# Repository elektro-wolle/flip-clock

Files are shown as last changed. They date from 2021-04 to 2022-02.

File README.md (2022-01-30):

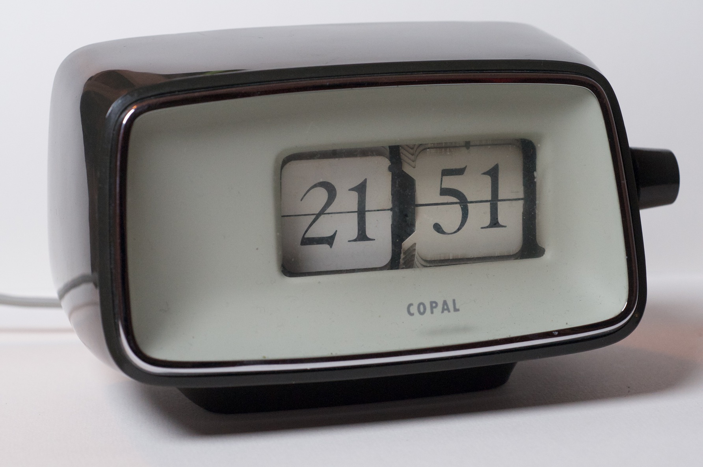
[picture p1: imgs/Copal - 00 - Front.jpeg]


Bei dieser schönen 60er-Jahre Uhr war der Synchronmotor defekt (lief nur
selten an, Versatz von 2h pro Tag). Ein Ersatz für diesen war nicht zu
finden, daher die High-Tech-Variante.

-   Synchronmotor durch Schrittmotor ersetzen

-   Zeit via NTP über einen ESP holen

-   Das Ganze so, dass es ein 1:1 Ersatz zu dem montierten Motor wird

# Herausforderungen

-   Einen Schrittmotor finden mit passendem Ritzel und passender Größe.

-   Der Schrittmotor mit passendem Ritzel ist für max. 5V ausgelegt, die
    üblichen StepSticks brauchen 8V.

-   Alles in das Gehäuse bekommen.

-   Erste Tests zeigten, dass für eine Minute eine unterschiedliche
    Anzahl an Schritten benötigt wird.

-   Keine Möglichkeit, das Umspringen der Minuten zu erkennen.

-   Spontane Abschaltungen bei Netzbetrieb.

# Lösungen

## Schrittmotor

AliExpress sei Dank: [Stepper-Motor mit 12 Zähnen und Modul
0,25](https://www.aliexpress.com/item/4001009328124.html).

## StepStick

Natürlich gibt es was von [Trinamic](https://www.trinamic.com) auf Basis
des [TMC2225
Datasheet](https://www.trinamic.com/fileadmin/assets/Products/ICs_Documents/TMC2225_Datasheet_Rev1.11.pdf).
Zum Beispiel [hier](https://www.amazon.de/dp/B08R3GFYTR).

## Platine produzieren

Millimetergenaues Ausmessen, KiCad, Aisler:

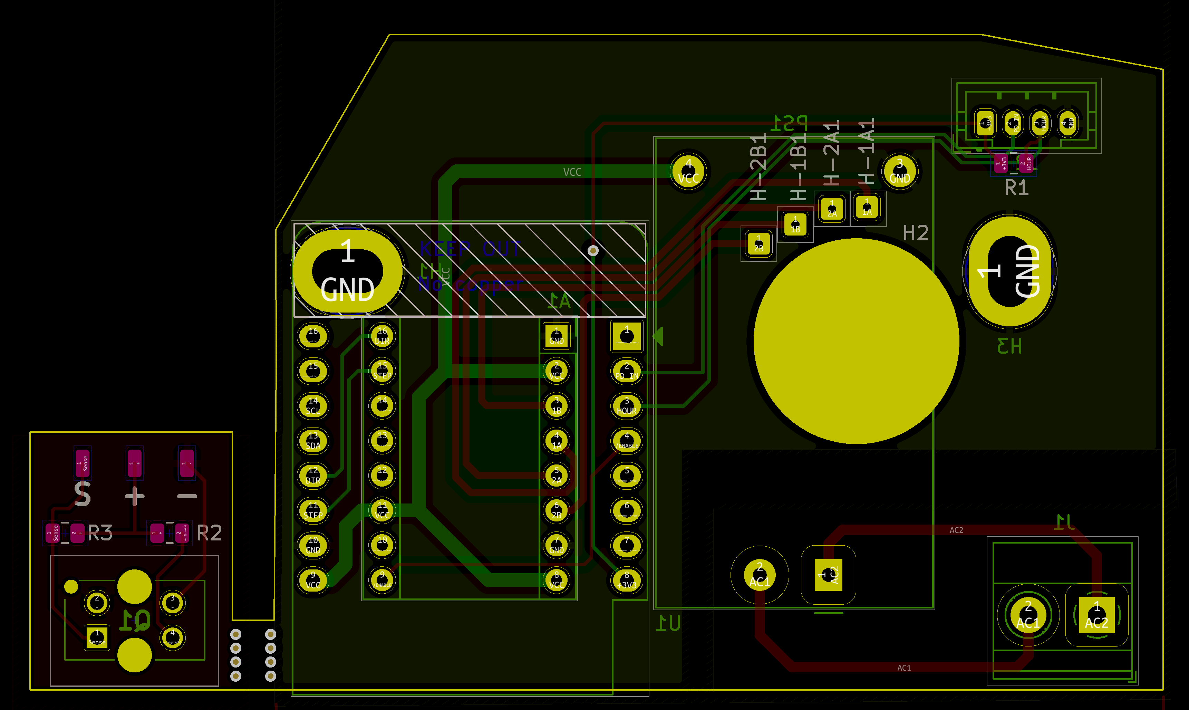
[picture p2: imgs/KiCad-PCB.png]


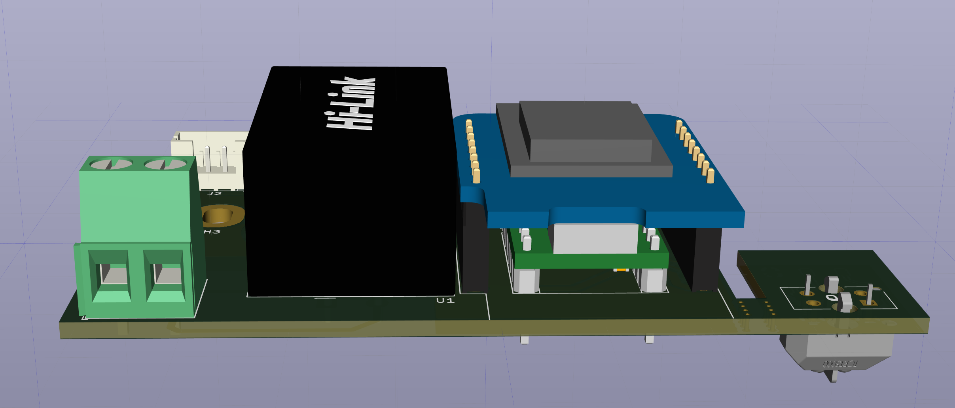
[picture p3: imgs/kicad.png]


## Schritte zählen

Aufgrund des doch sehr beschränkten Platzes, blieb nur die Möglichkeit
übrig, die bestehende Glimmmlampe auszubauen und stattdessen eine kleine
Reflex-Lichtschranke (TCRT-5000) anzubringen. Diese löst recht
zuverlässig auf, wenn sich ein Blatt der Minuten-Anzeige im Fallen
befindet.

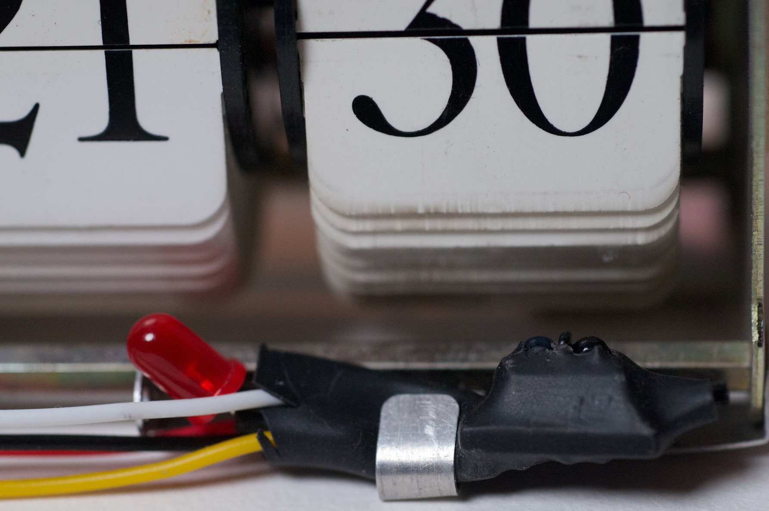
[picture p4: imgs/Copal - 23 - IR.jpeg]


## Spontane Resets

Ein 100uF Kondensator auf der 5V Schiene wirkt Wunder:

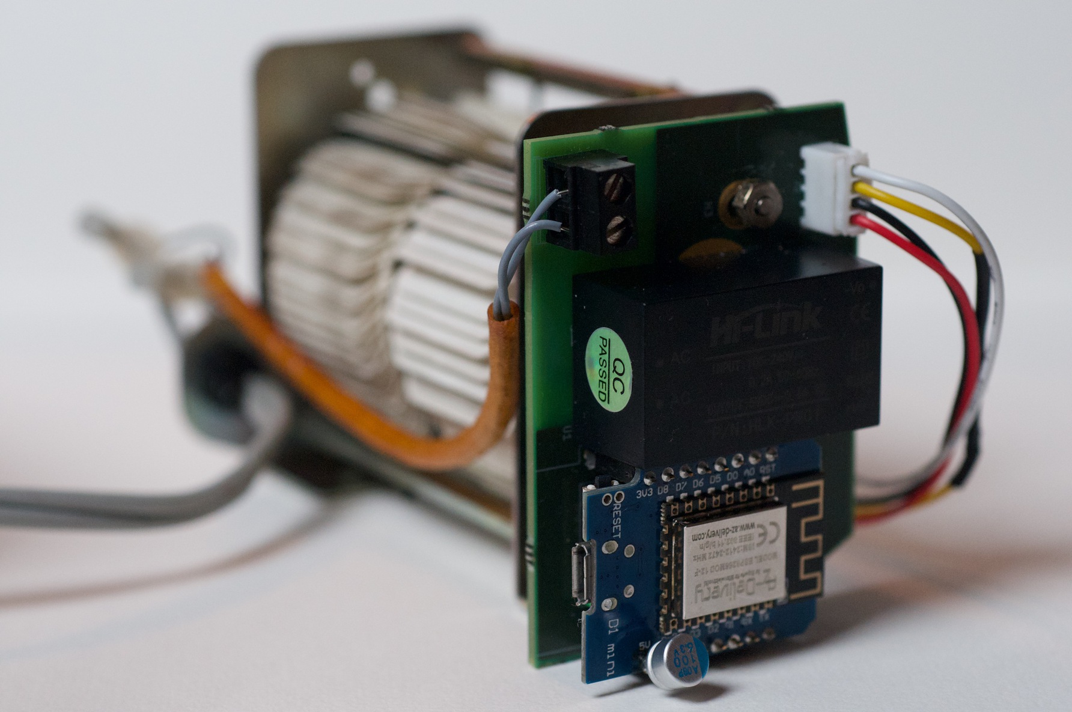
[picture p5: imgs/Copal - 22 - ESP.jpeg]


## Fertiger Aufbau

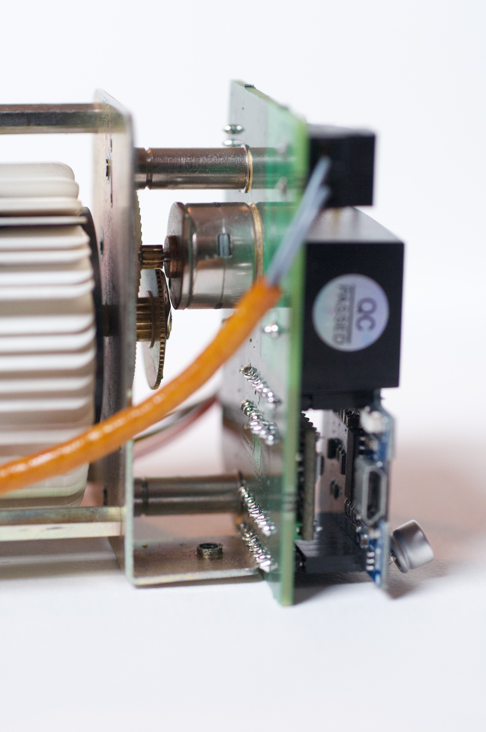
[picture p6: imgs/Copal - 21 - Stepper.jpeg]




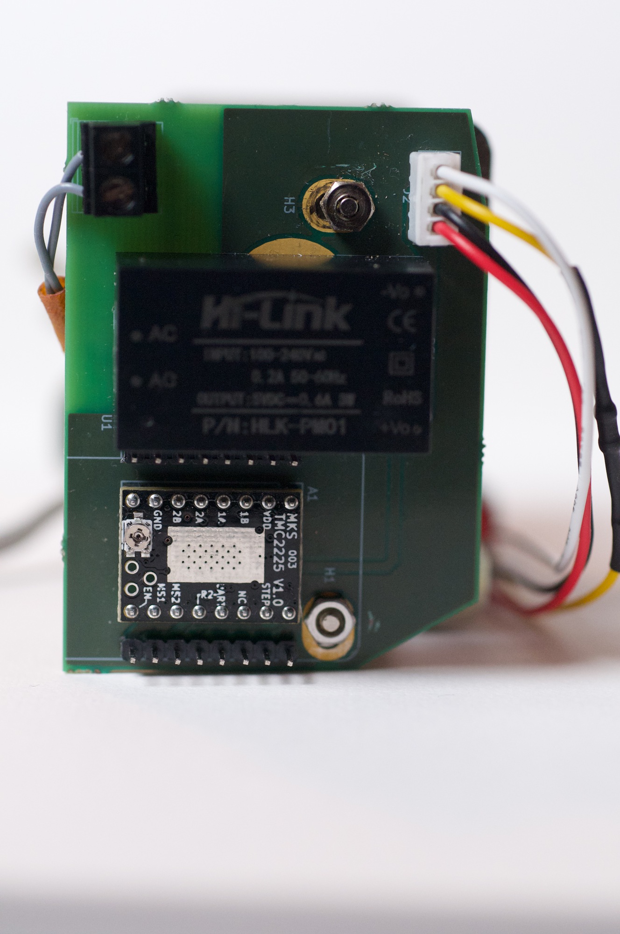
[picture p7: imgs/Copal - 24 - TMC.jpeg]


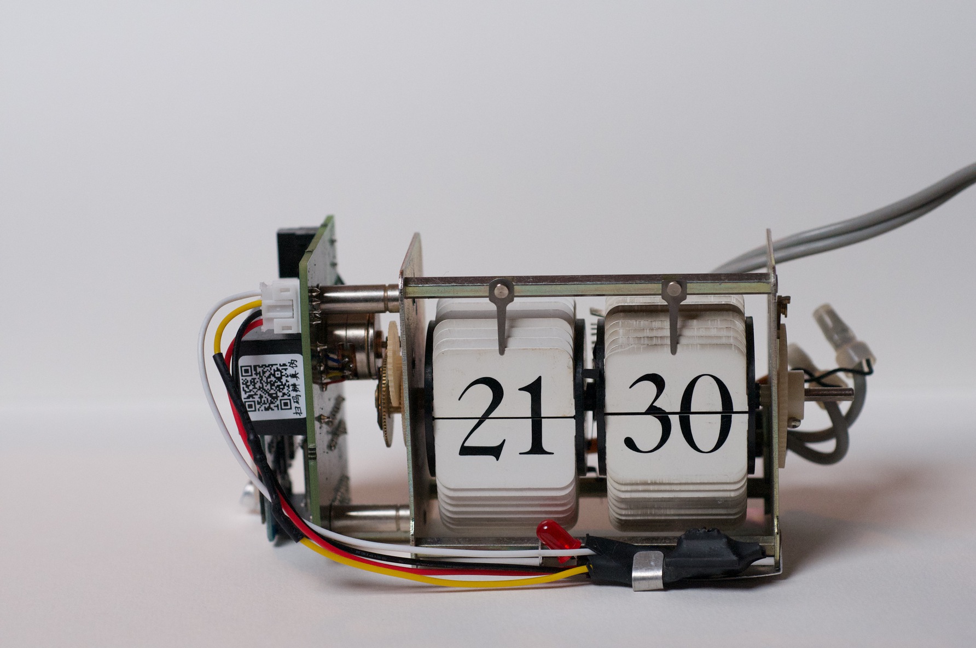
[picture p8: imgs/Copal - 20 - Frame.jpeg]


## Zusammenbau

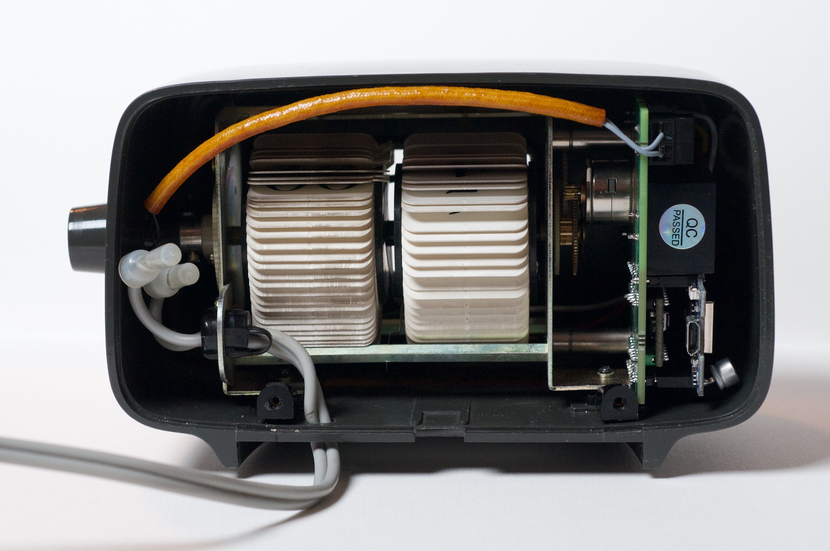
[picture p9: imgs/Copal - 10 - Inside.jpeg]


# Software

Kleines C++ Projekt mit platformio auf Basis der Bibliotheken:
[WiFiManager](https://github.com/tzapu/WiFiManager),
[AceTime](https://github.com/bxparks/AceTime),
[ESP_DoubleResetDetector](https://github.com/khoih-prog/ESP_DoubleResetDetector).

Lösung ist straight-forward: Intern wird die vermutlich angezeigte Zeit
(durch das Zählen via IR-Reflex-Lichtschranke) mit der via NTP
empfangenen Zeit verglichen und solange der Stepper-Motor aktiviert, bis
diese übereinstimmen.

Dabei eine Sonderbehandlung für kleine Abweichungen (bis 10 Minuten wird
einfach gewartet, bis die Zeit übereinstimmt) und in der Nacht (z.B. Bei
der Sommer-/Winterzeit-Umstellung müssten 23 Stunden nach vorne gestellt
werden).

Über eine minimale Web-Oberfläche kann bei Stromausfall oder ähnlichem
die tatsächlich angezeigte Uhrzeit angegeben werden. Code siehe
[Quellcode](sw/src/main.cpp).

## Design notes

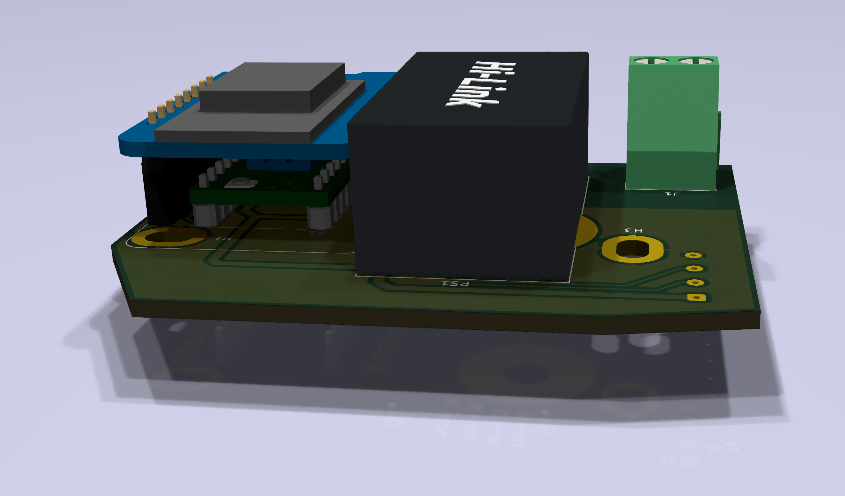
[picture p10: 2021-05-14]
hardware/flip-clock-front.png

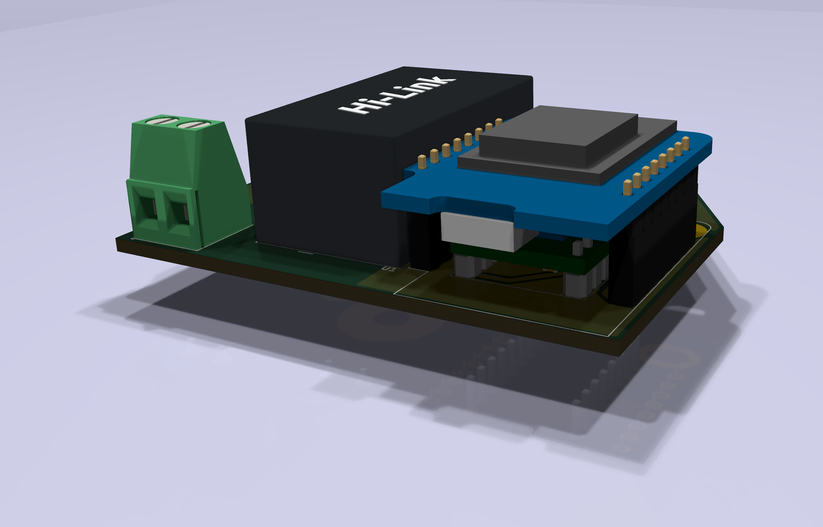
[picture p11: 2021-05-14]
hardware/flip-clock-rear.png

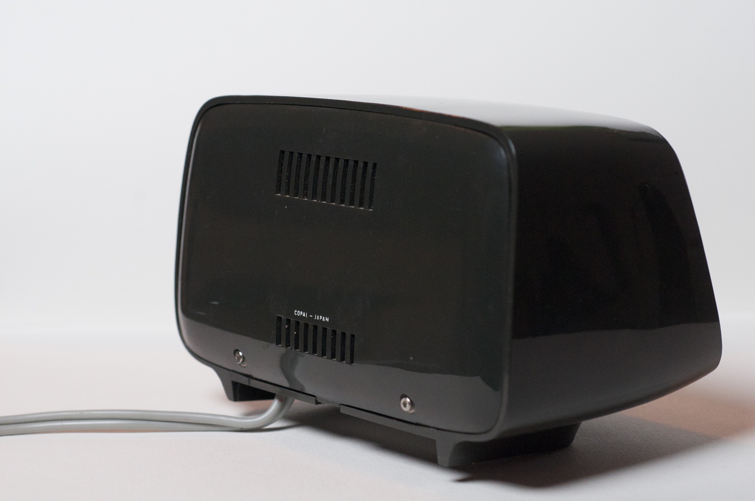
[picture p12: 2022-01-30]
imgs/Copal - 01 - Back.jpeg

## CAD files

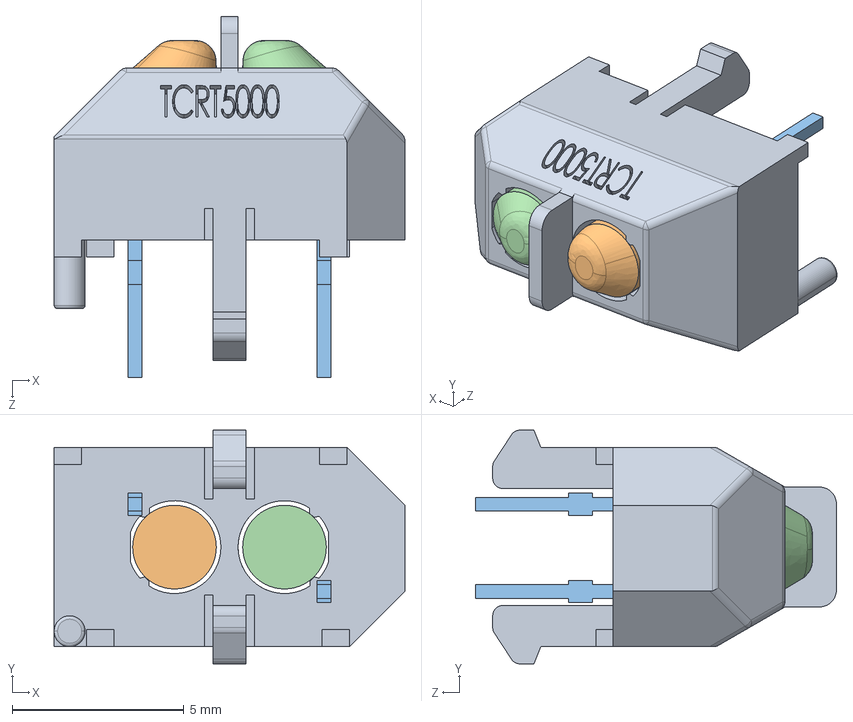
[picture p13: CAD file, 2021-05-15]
hardware/LIB_TCRT5000/TCRT5000/3D/TCRT5000.stp
10.2 x 6.80 x 10.5 mm

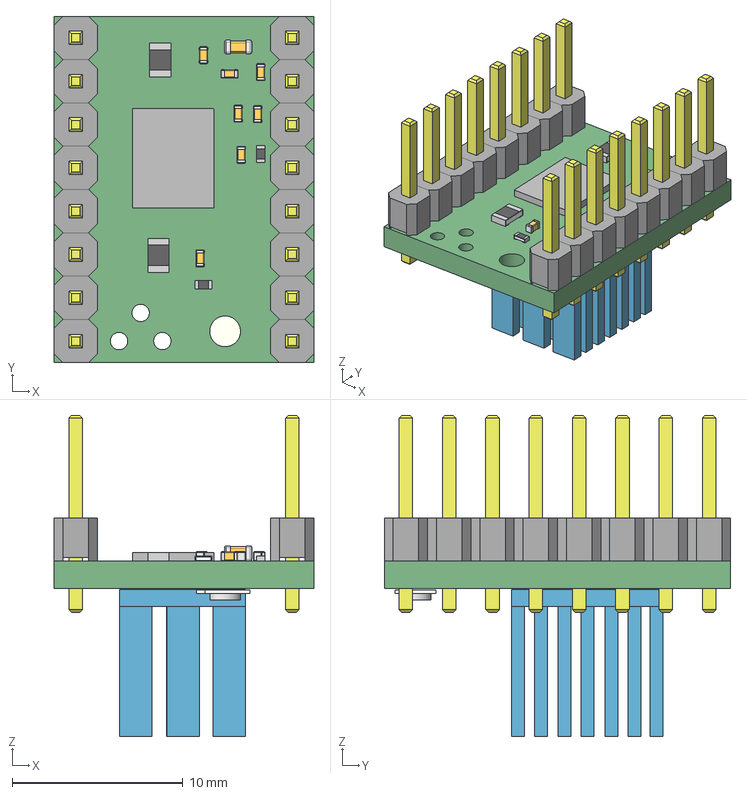
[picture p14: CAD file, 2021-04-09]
hardware/tmc2100.step
15.2 x 20.3 x 18.8 mm
Board
1x08 x 4
R0402 x 8
R0805 x 8
C0603 x 2
C0402 x 14
Extruded x 24

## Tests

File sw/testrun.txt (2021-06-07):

05:07:

begin
[rep=19,min=22,delta=11,avg=1], [rep=34,min=26,delta=201,avg=60], 
done after 34
05:08:

begin
[rep=35,min=26,delta=225,avg=118], 
done after 35
05:09:

begin
[rep=34,min=26,delta=206,avg=83], 
done after 34
05:10:

begin
[rep=0,min=14,delta=11,avg=6], [rep=34,min=29,delta=21,avg=3], [rep=35,min=111,delta=152,avg=104], 
done after 35
05:11:

begin
[rep=16,min=16,delta=14,avg=3], [rep=22,min=12,delta=19,avg=7], [rep=27,min=21,delta=21,avg=3], [rep=38,min=27,delta=213,avg=68], 
done after 38
05:12:

begin
[rep=1,min=20,delta=12,avg=1], [rep=6,min=14,delta=17,avg=5], [rep=12,min=16,delta=16,avg=5], [rep=18,min=20,delta=14,avg=1], [rep=35,min=28,delta=60,avg=7], [rep=36,min=125,delta=126,avg=79], 
done after 36
05:13:

begin
[rep=32,min=28,delta=155,avg=25], 
done after 32
05:14:

begin
[rep=33,min=18,delta=236,avg=122], 
done after 33
05:15:

begin
[rep=37,min=21,delta=224,avg=139], 
done after 37
05:16:

begin
[rep=26,min=23,delta=12,avg=1], [rep=34,min=25,delta=244,avg=169], 
done after 34
05:17:

begin
[rep=35,min=26,delta=228,avg=158], 
done after 35
05:18:

begin
[rep=8,min=17,delta=12,avg=2], [rep=32,min=29,delta=215,avg=103], 
done after 32
05:19:

begin
[rep=35,min=25,delta=192,avg=44], 
done after 35
05:20:

begin
[rep=26,min=15,delta=16,avg=5], [rep=31,min=22,delta=11,avg=1], [rep=37,min=24,delta=18,avg=3], [rep=40,min=28,delta=131,avg=17], 
done after 40
05:21:

begin
[rep=3,min=16,delta=16,avg=2], [rep=8,min=16,delta=12,avg=2], [rep=14,min=13,delta=19,avg=5], [rep=20,min=21,delta=19,avg=3], [rep=25,min=20,delta=18,avg=5], [rep=33,min=27,delta=151,avg=27], 
done after 33
05:22:

begin
[rep=34,min=30,delta=204,avg=51], 
done after 34
05:23:

begin
[rep=35,min=30,delta=115,avg=19], 
done after 35
05:24:

begin
[rep=37,min=29,delta=224,avg=127], 
done after 37
05:25:

begin
[rep=33,min=27,delta=203,avg=102], 
done after 33
05:26:

begin
[rep=0,min=12,delta=11,avg=7], [rep=33,min=23,delta=160,avg=29], 
done after 33
05:27:

begin
[rep=36,min=25,delta=159,avg=31], 
done after 36
05:28:

begin
[rep=37,min=25,delta=60,avg=11], [rep=38,min=124,delta=128,avg=78], 
done after 38
05:29:

begin
[rep=12,min=18,delta=19,avg=4], [rep=17,min=17,delta=13,avg=4], [rep=23,min=25,delta=15,avg=3], [rep=28,min=25,delta=17,avg=3], [rep=34,min=28,delta=212,avg=108], 
done after 34
05:30:

begin
[rep=0,min=12,delta=12,avg=6], [rep=8,min=17,delta=21,avg=11], [rep=33,min=29,delta=227,avg=112], 
done after 33
05:31:

begin
[rep=34,min=29,delta=219,avg=135], 
done after 34
05:32:

begin
[rep=36,min=28,delta=225,avg=155], 
done after 36
05:33:

begin
[rep=34,min=14,delta=190,avg=49], 
done after 34
05:34:

begin
[rep=34,min=35,delta=212,avg=78], 
done after 34
05:35:

begin
[rep=33,min=29,delta=20,avg=9], [rep=34,min=112,delta=136,avg=85], 
done after 34
05:36:

begin
[rep=4,min=17,delta=13,avg=2], [rep=32,min=32,delta=210,avg=79], 
done after 32
05:37:

begin
[rep=37,min=30,delta=213,avg=150], 
done after 37
05:38:

begin
[rep=3,min=18,delta=11,avg=2], [rep=8,min=19,delta=16,avg=1], [rep=14,min=20,delta=17,avg=4], [rep=20,min=25,delta=12,avg=3], [rep=25,min=32,delta=17,avg=2], [rep=35,min=32,delta=158,avg=27], 
done after 35
05:39:

begin
[rep=34,min=35,delta=191,avg=82], 
done after 34
05:40:

begin
[rep=34,min=39,delta=211,avg=131], 
done after 34
05:41:

begin
[rep=32,min=26,delta=208,avg=100], 
done after 32
05:42:

begin
[rep=34,min=20,delta=91,avg=15], 
done after 34
05:43:

begin
[rep=39,min=20,delta=138,avg=24], 
done after 39
05:44:

begin
[rep=32,min=19,delta=207,avg=85], 
done after 32
05:45:

begin
[rep=0,min=12,delta=12,avg=7], [rep=33,min=26,delta=30,avg=6], [rep=34,min=112,delta=121,avg=79], 
done after 34
05:46:

begin
[rep=0,min=13,delta=16,avg=6], [rep=36,min=21,delta=223,avg=106], 
done after 36
05:47:

begin
[rep=3,min=15,delta=17,avg=2], [rep=9,min=14,delta=12,avg=3], [rep=15,min=17,delta=14,avg=1], [rep=20,min=15,delta=20,avg=5], [rep=26,min=22,delta=12,avg=3], [rep=32,min=27,delta=16,avg=2], [rep=35,min=26,delta=126,avg=21], 
done after 35
05:48:

begin
[rep=34,min=24,delta=221,avg=148], 
done after 34
05:49:

begin
[rep=33,min=21,delta=169,avg=36], 
done after 33
05:50:

begin
[rep=21,min=12,delta=19,avg=9], [rep=33,min=43,delta=198,avg=144], 
done after 33
05:51:

begin
[rep=36,min=10,delta=216,avg=126], 
done after 36
05:52:

begin
[rep=34,min=24,delta=200,avg=54], 
done after 34
05:53:

begin
[rep=34,min=14,delta=124,avg=21], 
done after 34
05:54:

begin
[rep=32,min=19,delta=155,avg=30], 
done after 32
05:55:

begin
[rep=35,min=24,delta=208,avg=74], 
done after 35
05:56:

begin
[rep=3,min=14,delta=11,avg=3], [rep=8,min=15,delta=11,avg=1], [rep=14,min=14,delta=20,avg=3], [rep=20,min=11,delta=13,avg=5], [rep=25,min=16,delta=19,avg=3], [rep=31,min=18,delta=19,avg=6], [rep=37,min=22,delta=219,avg=87], 
done after 37
05:57:

begin
[rep=0,min=8,delta=24,avg=12], [rep=36,min=29,delta=220,avg=159], 
done after 36
05:58:

begin
[rep=20,min=21,delta=11,avg=1], [rep=33,min=21,delta=232,avg=158], 
done after 33
05:59:

begin
[rep=33,min=25,delta=175,avg=42], 
done after 33
06:00:

begin
[rep=32,min=23,delta=210,avg=53], 
done after 32
06:01:

begin
[rep=35,min=20,delta=12,avg=8], [rep=36,min=54,delta=190,avg=132], 
done after 36
06:02:

begin
[rep=33,min=21,delta=19,avg=9], [rep=34,min=103,delta=145,avg=89], 
done after 34
06:03:

begin
[rep=34,min=23,delta=207,avg=140], 
done after 34
06:04:

begin
[rep=16,min=17,delta=11,avg=1], [rep=35,min=19,delta=53,avg=10], [rep=36,min=130,delta=119,avg=69], 
done after 36
06:05:

begin
[rep=8,min=15,delta=13,avg=2], [rep=14,min=14,delta=19,avg=3], [rep=19,min=15,delta=12,avg=1], [rep=25,min=11,delta=12,avg=4], [rep=30,min=20,delta=18,avg=1], [rep=33,min=15,delta=215,avg=147], 
done after 33
06:06:

begin
[rep=41,min=20,delta=197,avg=50], 
done after 41
06:07:

begin
[rep=32,min=21,delta=13,avg=7], [rep=33,min=90,delta=151,avg=103], 
done after 33
06:08:

begin
[rep=31,min=26,delta=209,avg=63], 
done after 31
06:09:

begin
[rep=35,min=23,delta=209,avg=128], 
done after 35
06:10:

begin
[rep=34,min=28,delta=24,avg=3], [rep=35,min=118,delta=144,avg=99], 
done after 35
06:11:

begin
[rep=36,min=26,delta=215,avg=74], 
done after 36
06:12:

begin
[rep=34,min=27,delta=201,avg=48], 
done after 34
06:13:

begin
[rep=35,min=26,delta=208,avg=100], 
done after 35
06:14:

begin
[rep=0,min=12,delta=18,avg=7], [rep=5,min=17,delta=11,avg=2], [rep=11,min=13,delta=13,avg=2], [rep=17,min=12,delta=19,avg=2], [rep=22,min=12,delta=16,avg=2], [rep=34,min=11,delta=159,avg=29], 
done after 34
06:15:

begin
[rep=38,min=16,delta=225,avg=122], 
done after 38
06:16:

begin
[rep=32,min=29,delta=73,avg=9], [rep=33,min=146,delta=129,avg=80], 
done after 33
06:17:

begin
[rep=34,min=26,delta=218,avg=90], 
done after 34
06:18:

begin
[rep=34,min=21,delta=186,avg=36], 
done after 34
06:19:

begin
[rep=35,min=27,delta=189,avg=40], 
done after 35
06:20:

begin
[rep=0,min=13,delta=11,avg=6], [rep=36,min=33,delta=216,avg=81], 
done after 36
06:21:

begin
[rep=33,min=22,delta=214,avg=129], 
done after 33
06:22:

begin
[rep=27,min=23,delta=12,avg=2], [rep=37,min=25,delta=121,avg=21], 
done after 37
06:23:

begin
[rep=2,min=17,delta=20,avg=3], [rep=7,min=14,delta=12,avg=4], [rep=13,min=21,delta=11,avg=1], [rep=19,min=22,delta=16,avg=1], [rep=24,min=25,delta=15,avg=2], [rep=37,min=25,delta=216,avg=140], 
done after 37
06:24:

begin
[rep=33,min=20,delta=119,avg=18], 
done after 33
06:25:

begin
[rep=34,min=19,delta=197,avg=87], 
done after 34
06:26:

begin
[rep=27,min=21,delta=12,avg=1], [rep=35,min=15,delta=222,avg=80], 
done after 35
06:27:

begin
[rep=36,min=19,delta=217,avg=130], 
done after 36
06:28:

begin
[rep=33,min=26,delta=208,avg=60], 
done after 33
06:29:

begin
[rep=34,min=25,delta=205,avg=84], 
done after 34
06:30:

begin
[rep=36,min=30,delta=45,avg=8], [rep=37,min=124,delta=133,avg=79], 
done after 37
06:31:

begin
[rep=22,min=20,delta=12,avg=3], [rep=33,min=30,delta=16,avg=2], [rep=36,min=28,delta=217,avg=156], 
done after 36
06:32:

begin
[rep=3,min=18,delta=13,avg=5], [rep=34,min=34,delta=175,avg=27], 
done after 34
06:33:

begin
[rep=33,min=33,delta=198,avg=145], 
done after 33
06:34:

begin
[rep=35,min=35,delta=221,avg=158], 
done after 35
06:35:

begin
[rep=34,min=32,delta=97,avg=13], 
done after 34
06:36:

begin
[rep=34,min=26,delta=225,avg=128], 
done after 34
06:37:

begin
[rep=2,min=11,delta=13,avg=8], [rep=34,min=32,delta=207,avg=143], 
done after 34
06:38:

begin
[rep=33,min=30,delta=228,avg=154], 
done after 33
06:39:

begin
[rep=31,min=33,delta=18,avg=6], [rep=33,min=35,delta=201,avg=101], 
done after 33
06:40:

begin
[rep=4,min=14,delta=15,avg=5], [rep=10,min=16,delta=17,avg=2], [rep=15,min=13,delta=19,avg=6], [rep=21,min=20,delta=18,avg=5], [rep=32,min=34,delta=11,avg=3], [rep=36,min=34,delta=220,avg=109], 
done after 36
06:41:

begin
[rep=34,min=24,delta=88,avg=14], 
done after 34
06:42:

begin
[rep=35,min=24,delta=39,avg=9], [rep=36,min=127,delta=111,avg=68], 
done after 36
06:43:

begin
[rep=36,min=11,delta=137,avg=24], 
done after 36
06:44:

begin
[rep=32,min=19,delta=132,avg=25], 
done after 32
06:45:

begin
[rep=36,min=19,delta=194,avg=55], 
done after 36
06:46:

begin
[rep=35,min=88,delta=175,avg=124], 
done after 35
06:47:

begin
[rep=32,min=27,delta=126,avg=21], 
done after 32
06:48:

begin
[rep=32,min=19,delta=185,avg=42], 
done after 32
06:49:

begin
[rep=0,min=12,delta=20,avg=7], [rep=6,min=17,delta=17,avg=2], [rep=11,min=16,delta=18,avg=2], [rep=17,min=15,delta=12,avg=1], [rep=22,min=17,delta=17,avg=2], [rep=36,min=39,delta=193,avg=144], 
done after 36
06:50:

begin
[rep=35,min=13,delta=217,avg=60], 
done after 35
06:51:

begin
[rep=37,min=48,delta=189,avg=136], 
done after 37
06:52:

begin
[rep=32,min=16,delta=63,avg=8], [rep=33,min=134,delta=112,avg=71], 
done after 33
06:53:

begin
[rep=32,min=17,delta=122,avg=20], 
done after 32
06:54:

begin
[rep=34,min=8,delta=219,avg=125], 
done after 34
06:55:

begin
[rep=35,min=24,delta=59,avg=11], [rep=36,min=140,delta=103,avg=66], 
done after 36
06:56:

begin
[rep=34,min=18,delta=129,avg=23], 
done after 34
06:57:

begin
[rep=16,min=18,delta=18,avg=3], [rep=18,min=14,delta=11,avg=8], [rep=22,min=25,delta=17,avg=2], [rep=28,min=29,delta=12,avg=1], [rep=33,min=26,delta=182,avg=39], 
done after 33
06:58:

begin
[rep=0,min=12,delta=22,avg=8], [rep=6,min=17,delta=17,avg=3], [rep=34,min=20,delta=238,avg=144], 
done after 34
06:59:

begin
[rep=36,min=23,delta=14,avg=9], [rep=37,min=84,delta=146,avg=106], 
done after 37
07:00:

begin
[rep=33,min=32,delta=221,avg=122], 
done after 33
07:01:

begin
[rep=36,min=22,delta=226,avg=149], 
done after 36
07:02:

begin
[rep=32,min=27,delta=226,avg=146], 
done after 32
07:03:

begin
[rep=33,min=18,delta=33,avg=8], [rep=34,min=105,delta=124,avg=77], 
done after 34
07:04:

begin
[rep=35,min=21,delta=226,avg=126], 
done after 35
07:05:

begin
[rep=36,min=55,delta=182,avg=129], 
done after 36
07:06:

begin
[rep=0,min=13,delta=20,avg=6], [rep=6,min=19,delta=19,avg=4], [rep=11,min=16,delta=11,avg=2], [rep=17,min=14,delta=12,avg=4], [rep=23,min=18,delta=16,avg=2], [rep=28,min=22,delta=11,avg=2], [rep=34,min=26,delta=17,avg=2], [rep=37,min=22,delta=204,avg=58], 
done after 37
07:07:

begin
[rep=34,min=20,delta=193,avg=50], 
done after 34
07:08:

begin
[rep=33,min=22,delta=106,avg=16], 
done after 33
07:09:

begin
[rep=37,min=21,delta=34,avg=5], [rep=38,min=114,delta=124,avg=91], 
done after 38
07:10:

begin
[rep=33,min=19,delta=226,avg=69], 
done after 33
07:11:

begin
[rep=33,min=19,delta=205,avg=52], 
done after 33
07:12:

begin
[rep=36,min=23,delta=227,avg=150], 
done after 36
07:13:

begin
[rep=35,min=37,delta=208,avg=97], 
done after 35
07:14:

begin
[rep=26,min=14,delta=11,avg=4], [rep=32,min=31,delta=11,avg=2], [rep=33,min=31,delta=230,avg=83], 
done after 33
07:15:

begin
[rep=4,min=17,delta=13,avg=2], [rep=10,min=14,delta=11,avg=2], [rep=34,min=17,delta=35,avg=4], [rep=35,min=122,delta=124,avg=87], 
done after 35
07:16:

begin
[rep=33,min=22,delta=193,avg=38], 
done after 33
07:17:

begin
[rep=4,min=16,delta=11,avg=1], [rep=15,min=15,delta=12,avg=1], [rep=39,min=24,delta=76,avg=10], [rep=40,min=133,delta=121,avg=78], 
done after 40
07:18:

begin
[rep=33,min=26,delta=218,avg=92], 
done after 33
07:19:

begin
[rep=33,min=23,delta=176,avg=34], 
done after 33
07:20:

begin
[rep=5,min=16,delta=11,avg=1], [rep=36,min=28,delta=229,avg=154], 
done after 36
07:21:

begin
[rep=36,min=26,delta=194,avg=73], 
done after 36
07:22:

begin
[rep=34,min=27,delta=204,avg=51], 
done after 34
07:23:

begin
[rep=29,min=18,delta=13,avg=5], [rep=34,min=21,delta=216,avg=128], 
done after 34
07:24:

begin
[rep=1,min=14,delta=19,avg=6], [rep=7,min=16,delta=17,avg=2], [rep=12,min=14,delta=14,avg=3], [rep=18,min=14,delta=14,avg=4], [rep=24,min=12,delta=21,avg=7], [rep=29,min=23,delta=16,avg=1], [rep=35,min=33,delta=12,avg=2], [rep=36,min=26,delta=215,avg=76], 
done after 36
07:25:

begin
[rep=37,min=22,delta=208,avg=108], 
done after 37
07:26:

begin
[rep=34,min=22,delta=64,avg=12], [rep=35,min=116,delta=137,avg=89], 
done after 35
07:27:

begin
[rep=33,min=24,delta=212,avg=142], 
done after 33
07:28:

begin
[rep=34,min=25,delta=212,avg=87], 
done after 34
07:29:

begin
[rep=36,min=26,delta=213,avg=145], 
done after 36
07:30:

begin
[rep=35,min=31,delta=230,avg=145], 
done after 35
07:31:

begin
[rep=33,min=27,delta=222,avg=157], 
done after 33
07:32:

begin
[rep=34,min=28,delta=228,avg=124], 
done after 34
07:33:

begin
[rep=10,min=15,delta=15,avg=1], [rep=16,min=13,delta=23,avg=7], [rep=22,min=21,delta=16,avg=2], [rep=27,min=23,delta=19,avg=4], [rep=33,min=34,delta=16,avg=2], [rep=35,min=33,delta=29,avg=5], [rep=36,min=124,delta=110,avg=70], 
done after 36
07:34:

begin
[rep=3,min=19,delta=11,avg=1], [rep=37,min=32,delta=216,avg=79], 
done after 37
07:35:

begin
[rep=33,min=31,delta=88,avg=11], 
done after 33
07:36:

begin
[rep=0,min=12,delta=11,avg=7], [rep=32,min=32,delta=196,avg=45], 
done after 32
07:37:

begin
[rep=33,min=28,delta=45,avg=10], [rep=34,min=128,delta=117,avg=69], 
done after 34
07:38:

begin
[rep=33,min=25,delta=232,avg=145], 
done after 33
07:39:

begin
[rep=35,min=30,delta=89,avg=14], 
done after 35
07:40:

begin
[rep=35,min=36,delta=26,avg=3], [rep=36,min=95,delta=158,avg=95], 
done after 36
07:41:

begin
[rep=32,min=25,delta=218,avg=113], 
done after 32
07:42:

begin
[rep=7,min=15,delta=15,avg=3], [rep=13,min=16,delta=12,avg=2], [rep=19,min=15,delta=22,avg=6], [rep=24,min=19,delta=16,avg=2], [rep=30,min=21,delta=18,avg=3], [rep=32,min=19,delta=159,avg=31], 
done after 32
07:43:

begin
[rep=41,min=13,delta=205,avg=136], 
done after 41
07:44:

begin
[rep=34,min=15,delta=60,avg=9], [rep=35,min=127,delta=114,avg=80], 
done after 35
07:45:

begin
[rep=33,min=24,delta=123,avg=21], 
done after 33
07:46:

begin
[rep=33,min=20,delta=134,avg=22], 
done after 33
07:47:

begin
[rep=33,min=25,delta=183,avg=51], 
done after 33
07:48:

begin
[rep=34,min=22,delta=195,avg=47], 
done after 34
07:49:

begin
[rep=35,min=15,delta=28,avg=5], [rep=36,min=96,delta=136,avg=98], 
done after 36
07:50:

begin
[rep=33,min=11,delta=236,avg=165], 
done after 33
07:51:

begin
[rep=2,min=16,delta=16,avg=3], [rep=8,min=14,delta=23,avg=6], [rep=14,min=18,delta=16,avg=1], [rep=19,min=13,delta=23,avg=6], [rep=25,min=21,delta=14,avg=4], [rep=33,min=22,delta=87,avg=13], 
done after 33
07:52:

begin
[rep=34,min=15,delta=215,avg=87], 
done after 34
07:53:

begin
[rep=37,min=17,delta=25,avg=8], [rep=38,min=97,delta=139,avg=103], 
done after 38
07:54:

begin
[rep=34,min=14,delta=232,avg=140], 
done after 34
07:55:

begin
[rep=34,min=24,delta=174,avg=35], 
done after 34
07:56:

begin
[rep=33,min=20,delta=230,avg=158], 
done after 33
07:57:

begin
[rep=11,min=21,delta=12,avg=1], [rep=35,min=35,delta=125,avg=20], 
done after 35
07:58:

begin
[rep=33,min=20,delta=223,avg=109], 
done after 33
07:59:

begin
[rep=33,min=27,delta=11,avg=5], [rep=34,min=33,delta=17,avg=1], [rep=36,min=26,delta=191,avg=93], 
done after 36
08:00:

begin
[rep=3,min=15,delta=18,avg=4], [rep=9,min=12,delta=22,avg=7], [rep=26,min=22,delta=11,avg=6], [rep=31,min=31,delta=13,avg=2], [rep=32,min=28,delta=218,avg=143], 
done after 32
08:01:

begin
[rep=34,min=17,delta=186,avg=40], 
done after 34
08:02:

begin
[rep=33,min=23,delta=226,avg=145], 
done after 33
08:03:

begin
[rep=0,min=14,delta=11,avg=6], [rep=17,min=9,delta=12,avg=1], [rep=38,min=-2,delta=213,avg=112], 
done after 38
08:04:

begin
[rep=36,min=19,delta=165,avg=30], 
done after 36
08:05:

begin
[rep=33,min=20,delta=215,avg=138], 
done after 33
08:06:

begin
[rep=0,min=11,delta=12,avg=7], [rep=37,min=22,delta=211,avg=76], 
done after 37
08:07:

begin
[rep=34,min=14,delta=208,avg=87], 
done after 34
08:08:

begin
[rep=34,min=22,delta=11,avg=6], [rep=35,min=47,delta=204,avg=146], 
done after 35
08:09:

begin
[rep=7,min=19,delta=12,avg=2], [rep=13,min=15,delta=18,avg=5], [rep=19,min=19,delta=16,avg=1], [rep=30,min=22,delta=16,avg=2], [rep=34,min=22,delta=209,avg=91], 
done after 34
08:10:

begin
[rep=1,min=19,delta=15,avg=1], [rep=7,min=12,delta=19,avg=4], [rep=13,min=10,delta=12,avg=4], [rep=35,min=23,delta=238,avg=126], 
done after 35
08:11:

begin
[rep=36,min=24,delta=171,avg=34], 
done after 36
08:12:

begin
[rep=36,min=20,delta=144,avg=21], 
done after 36
08:13:

begin
[rep=33,min=25,delta=211,avg=151], 
done after 33
08:14:

begin
[rep=31,min=17,delta=110,avg=14], 
done after 31
08:15:

begin
[rep=38,min=19,delta=223,avg=170], 
done after 38
08:16:

begin
[rep=34,min=54,delta=216,avg=159], 
done after 34
08:17:

begin
[rep=34,min=23,delta=78,avg=11], [rep=35,min=120,delta=136,avg=85], 
done after 35
08:18:

begin
[rep=11,min=12,delta=11,avg=4], [rep=23,min=21,delta=12,avg=2], [rep=28,min=24,delta=22,avg=5], [rep=32,min=25,delta=234,avg=163], 
done after 32
08:19:

begin
[rep=2,min=20,delta=15,avg=2], [rep=7,min=15,delta=18,avg=2], [rep=34,min=21,delta=122,avg=18], 
done after 34
08:20:

begin
[rep=41,min=30,delta=229,avg=115], 
done after 41
08:21:

begin
[rep=33,min=25,delta=11,avg=6], [rep=34,min=42,delta=200,avg=137], 
done after 34
08:22:

begin
[rep=33,min=28,delta=203,avg=50], 
done after 33
08:23:

begin
[rep=36,min=26,delta=214,avg=144], 
done after 36
08:24:

begin
[rep=36,min=30,delta=222,avg=104], 
done after 36
08:25:

begin
[rep=33,min=24,delta=197,avg=83], 
done after 33
08:26:

begin
[rep=33,min=18,delta=13,avg=9], [rep=34,min=44,delta=208,avg=152], 
done after 34
08:27:

begin
[rep=3,min=19,delta=13,avg=1], [rep=9,min=15,delta=22,avg=6], [rep=20,min=16,delta=18,avg=5], [rep=26,min=22,delta=15,avg=2], [rep=31,min=22,delta=20,avg=7], [rep=36,min=23,delta=203,avg=65], 
done after 36
08:28:

begin
[rep=1,min=19,delta=18,avg=2], [rep=37,min=28,delta=210,avg=67], 
done after 37
08:29:

begin
[rep=34,min=25,delta=121,avg=16], 
done after 34
08:30:

begin
[rep=33,min=29,delta=194,avg=40], 
done after 33
08:31:

begin
[rep=34,min=28,delta=30,avg=4], [rep=35,min=120,delta=127,avg=83], 
done after 35
08:32:

begin
[rep=35,min=28,delta=160,avg=25], 
done after 35
08:33:

begin
[rep=34,min=28,delta=199,avg=52], 
done after 34
08:34:

begin
[rep=34,min=33,delta=227,avg=141], 
done after 34
08:35:

begin
[rep=33,min=32,delta=224,avg=108], 
done after 33
08:36:

begin
[rep=8,min=25,delta=15,avg=2], [rep=20,min=30,delta=11,avg=1], [rep=25,min=31,delta=17,avg=3], [rep=31,min=41,delta=15,avg=3], [rep=32,min=36,delta=169,avg=33], 
done after 32
08:37:

begin
[rep=5,min=14,delta=18,avg=2], [rep=37,min=28,delta=211,avg=109], 
done after 37
08:38:

begin
[rep=36,min=29,delta=226,avg=135], 
done after 36
08:39:

begin
[rep=34,min=-5,delta=206,avg=121], 
done after 34
08:40:

begin
[rep=34,min=43,delta=218,avg=143], 
done after 34
08:41:

begin
[rep=31,min=27,delta=100,avg=16], 
done after 31
08:42:

begin
[rep=35,min=18,delta=204,avg=74], 
done after 35
08:43:

begin
[rep=0,min=20,delta=11,avg=8], [rep=39,min=44,delta=169,avg=38], 
done after 39
08:44:

begin
[rep=17,min=15,delta=18,avg=5], [rep=18,min=10,delta=22,avg=7], [rep=32,min=17,delta=222,avg=146], 
done after 32
08:45:

begin
[rep=14,min=12,delta=12,avg=4], [rep=15,min=16,delta=19,avg=1], [rep=20,min=19,delta=12,avg=1], [rep=26,min=19,delta=19,avg=5], [rep=31,min=24,delta=20,avg=4], [rep=32,min=27,delta=19,avg=2], [rep=33,min=23,delta=196,avg=75], 
done after 33
08:46:

begin
[rep=4,min=15,delta=16,avg=3], [rep=36,min=19,delta=239,avg=156], 
done after 36
08:47:

begin
[rep=35,min=27,delta=185,avg=56], 
done after 35
08:48:

begin
[rep=1,min=19,delta=13,avg=1], [rep=34,min=24,delta=207,avg=93], 
done after 34
08:49:

begin
[rep=34,min=17,delta=220,avg=129], 
done after 34
08:50:

begin
[rep=33,min=19,delta=233,avg=144], 
done after 33
08:51:

begin
[rep=35,min=15,delta=12,avg=6], [rep=36,min=32,delta=201,avg=144], 
done after 36
08:52:

begin
[rep=34,min=19,delta=209,avg=65], 
done after 34
08:53:

begin
[rep=34,min=14,delta=187,avg=46], 
done after 34
08:54:

begin
[rep=16,min=21,delta=14,avg=1], [rep=27,min=24,delta=13,avg=2], [rep=32,min=19,delta=113,avg=21], 
done after 32
08:55:

begin
[rep=1,min=19,delta=19,avg=3], [rep=6,min=16,delta=13,avg=2], [rep=12,min=28,delta=18,avg=3], [rep=35,min=40,delta=204,avg=96], 
done after 35
08:56:

begin
[rep=36,min=21,delta=220,avg=90], 
done after 36
08:57:

begin
[rep=36,min=28,delta=181,avg=39], 
done after 36
08:58:

begin
[rep=34,min=21,delta=231,avg=168], 
done after 34
08:59:

begin
[rep=33,min=27,delta=188,avg=86], 
done after 33
09:00:

begin
[rep=19,min=21,delta=11,avg=2], [rep=33,min=27,delta=224,avg=150], 
done after 33
09:01:

begin
[rep=35,min=25,delta=218,avg=143], 
done after 35
09:02:

begin
[rep=2,min=18,delta=12,avg=1], [rep=33,min=8,delta=112,avg=16], 
done after 33
09:03:

begin
[rep=31,min=15,delta=14,avg=2], [rep=36,min=12,delta=216,avg=122], 
done after 36
09:04:

begin
[rep=0,min=11,delta=19,avg=6], [rep=6,min=17,delta=18,avg=4], [rep=12,min=13,delta=17,avg=2], [rep=36,min=21,delta=212,avg=87], 
done after 36
09:05:

begin
[rep=33,min=19,delta=75,avg=13], [rep=34,min=124,delta=110,avg=69], 
done after 34
09:06:

begin
[rep=41,min=18,delta=13,avg=10], [rep=42,min=110,delta=133,avg=89], 
done after 42
09:07:

begin
[rep=31,min=21,delta=204,avg=72], 
done after 31
09:08:

begin
[rep=4,min=16,delta=11,avg=1], [rep=31,min=24,delta=209,avg=76], 
done after 31
09:09:

begin
[rep=34,min=21,delta=128,avg=20], 
done after 34
09:10:

begin
[rep=36,min=24,delta=236,avg=156], 
done after 36
09:11:

begin
[rep=36,min=44,delta=213,avg=159], 
done after 36
09:12:

begin
[rep=14,min=27,delta=20,avg=9], [rep=20,min=28,delta=19,avg=6], [rep=25,min=36,delta=20,avg=2], [rep=31,min=42,delta=16,avg=2], [rep=34,min=43,delta=48,avg=5], [rep=35,min=154,delta=114,avg=71], 
done after 35
09:13:

begin
[rep=2,min=18,delta=17,avg=2], [rep=35,min=27,delta=212,avg=148], 
done after 35
09:14:

begin
[rep=33,min=14,delta=226,avg=86], 
done after 33
09:15:

begin
[rep=37,min=17,delta=127,avg=16], 
done after 37
09:16:

begin
[rep=32,min=25,delta=23,avg=7], [rep=33,min=118,delta=154,avg=103], 
done after 33
09:17:

begin
[rep=34,min=23,delta=229,avg=117], 
done after 34
09:18:

begin
[rep=34,min=32,delta=187,avg=38], 
done after 34
09:19:

begin
[rep=35,min=25,delta=186,avg=40], 
done after 35
09:20:

begin
[rep=36,min=35,delta=91,avg=9], 
done after 36
09:21:

begin
[rep=7,min=10,delta=17,avg=4], [rep=12,min=8,delta=16,avg=3], [rep=18,min=11,delta=15,avg=3], [rep=24,min=17,delta=12,avg=2], [rep=29,min=23,delta=17,avg=3], [rep=33,min=24,delta=190,avg=53], 
done after 33
09:22:

begin
[rep=38,min=27,delta=225,avg=143], 
done after 38
09:23:

begin
[rep=36,min=32,delta=196,avg=81], 
done after 36
09:24:

begin
[rep=34,min=62,delta=193,avg=135], 
done after 34
09:25:

begin
[rep=33,min=22,delta=195,avg=84], 
done after 33
09:26:

begin
[rep=35,min=20,delta=206,avg=50], 
done after 35
09:27:

begin
[rep=36,min=24,delta=213,avg=135], 
done after 36
09:28:

begin
[rep=33,min=29,delta=196,avg=47], 
done after 33
09:29:
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

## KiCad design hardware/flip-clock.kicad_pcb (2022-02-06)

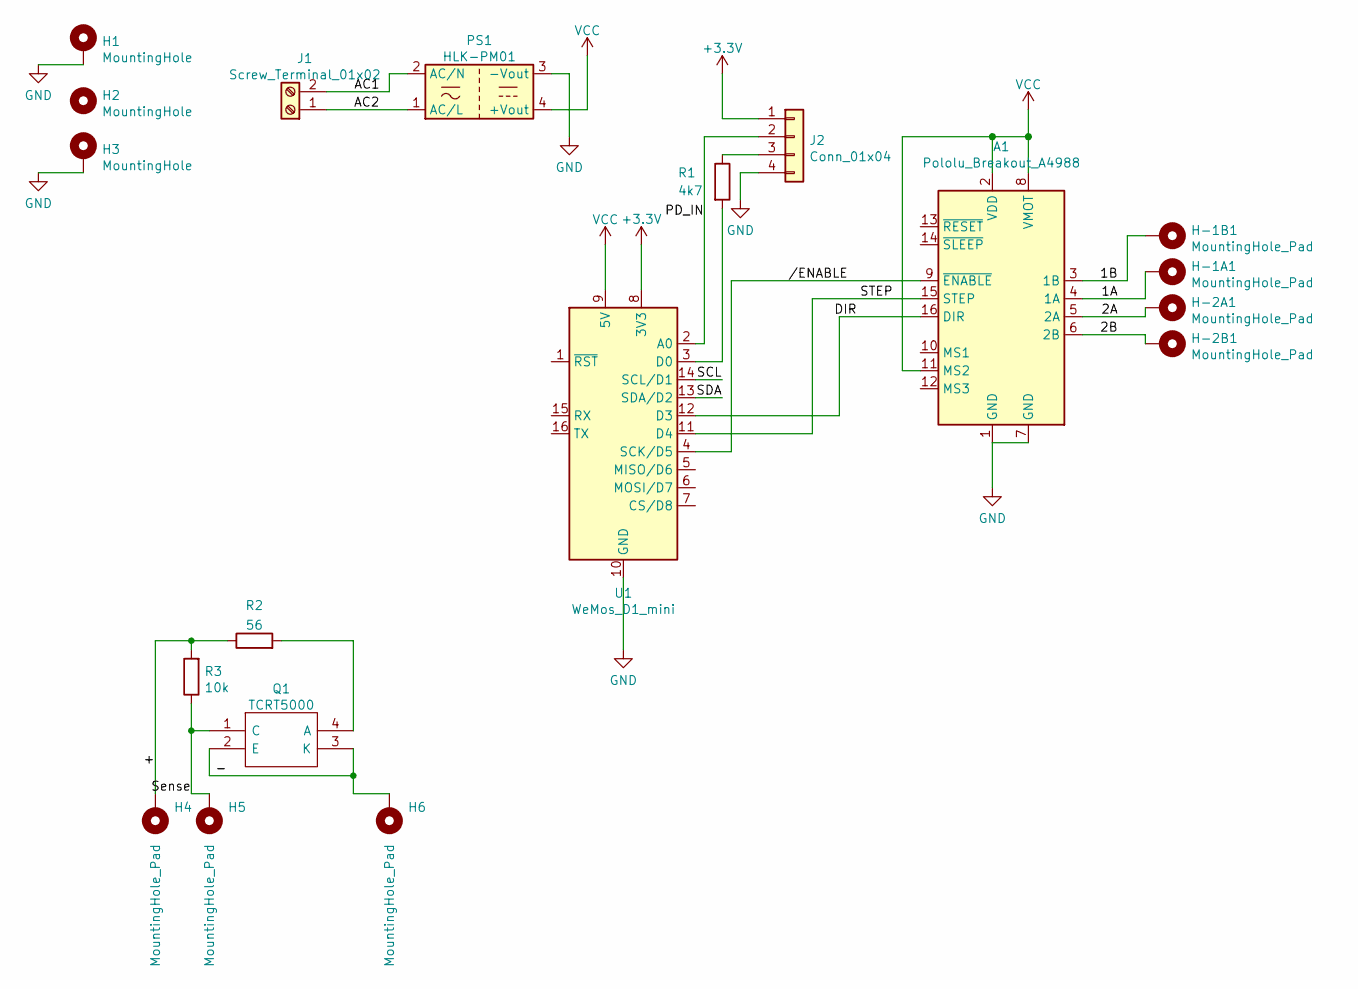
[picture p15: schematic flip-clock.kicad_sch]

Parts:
A1: Pololu_Breakout_A4988; Pololu_Breakout-16_15.2x20.3mm
H1, H3: MountingHole; MountingHole_3.2mm_M3_Pad
H2: MountingHole; MountingHole_5.3mm_M5
H4, H5, H6: MountingHole_Pad; SolderWirePad_1x01_SMD_1x2mm
H-1A1, H-1B1, H-2A1, H-2B1: MountingHole_Pad; SolderWire-0.1sqmm_1x01_D0.4mm_OD1mm
J1: Screw_Terminal_01x02; TerminalBlock_Phoenix_MKDS-1,5-2_1x02_P5.00mm_Horizontal
J2: Conn_01x04; JST_PH_B4B-PH-K_1x04_P2.00mm_Vertical
PS1: HLK-PM01; Converter_ACDC_HiLink_HLK-PMxx
Q1: TCRT5000; Manufacturer_Part_Number TCRT5000; Mouser Part Number 782-TCRT5000
R1: 4k7; R_0805_2012Metric
R2: 56; R_0805_2012Metric
R3: 10k; R_0805_2012Metric
U1: WeMos_D1_mini; WEMOS_D1_mini_light

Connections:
+3V3: J2.1, U1.8 (3V3)
/1A: A1.4 (1A), H-1A1.1
/1B: A1.3 (1B), H-1B1.1
/2A: A1.5 (2A), H-2A1.1
/2B: A1.6 (2B), H-2B1.1
/+: H4.1, R2.1, R3.2
/-: H6.1, Q1.2 (E), Q1.3 (K)
/AC1: J1.2, PS1.2 (AC/N)
/AC2: J1.1, PS1.1 (AC/L)
/DIR: A1.16 (DIR), U1.12 (D3)
/PD_IN: J2.2, U1.2 (A0)
/SCL: U1.14 (SCL/D1)
/SDA: U1.13 (SDA/D2)
/STEP: A1.15 (STEP), U1.11 (D4)
/Sense: H5.1, Q1.1 (C), R3.1
//ENABLE: A1.9 (~ENABLE), U1.4 (SCK/D5)
GND: A1.1 (GND), A1.7 (GND), H1.1, H3.1, J2.4, PS1.3 (-Vout), U1.10 (GND)
unnamed: J2.3, R1.1
unnamed: Q1.4 (A), R2.2
unnamed: R1.2, U1.3 (D0)
VCC: A1.2 (VDD), A1.8 (VMOT), A1.11 (MS2), PS1.4 (+Vout), U1.9 (5V)

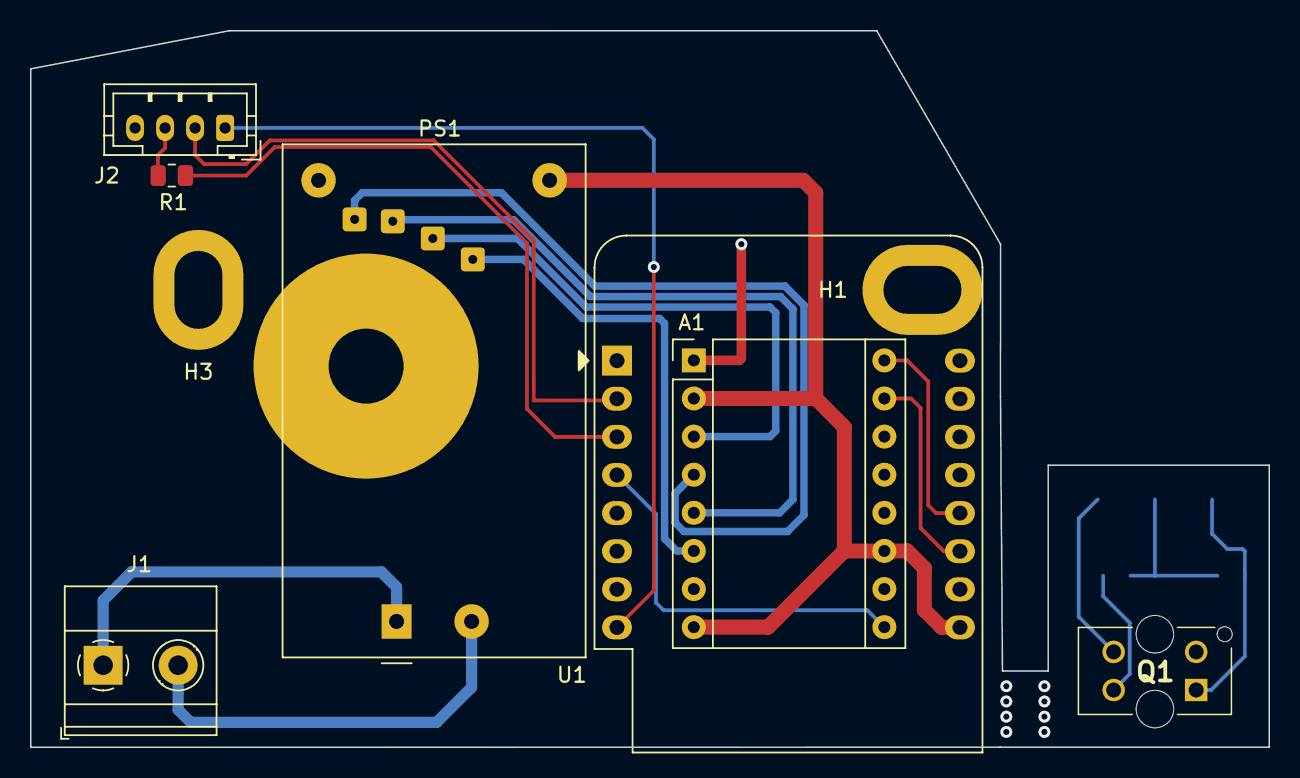
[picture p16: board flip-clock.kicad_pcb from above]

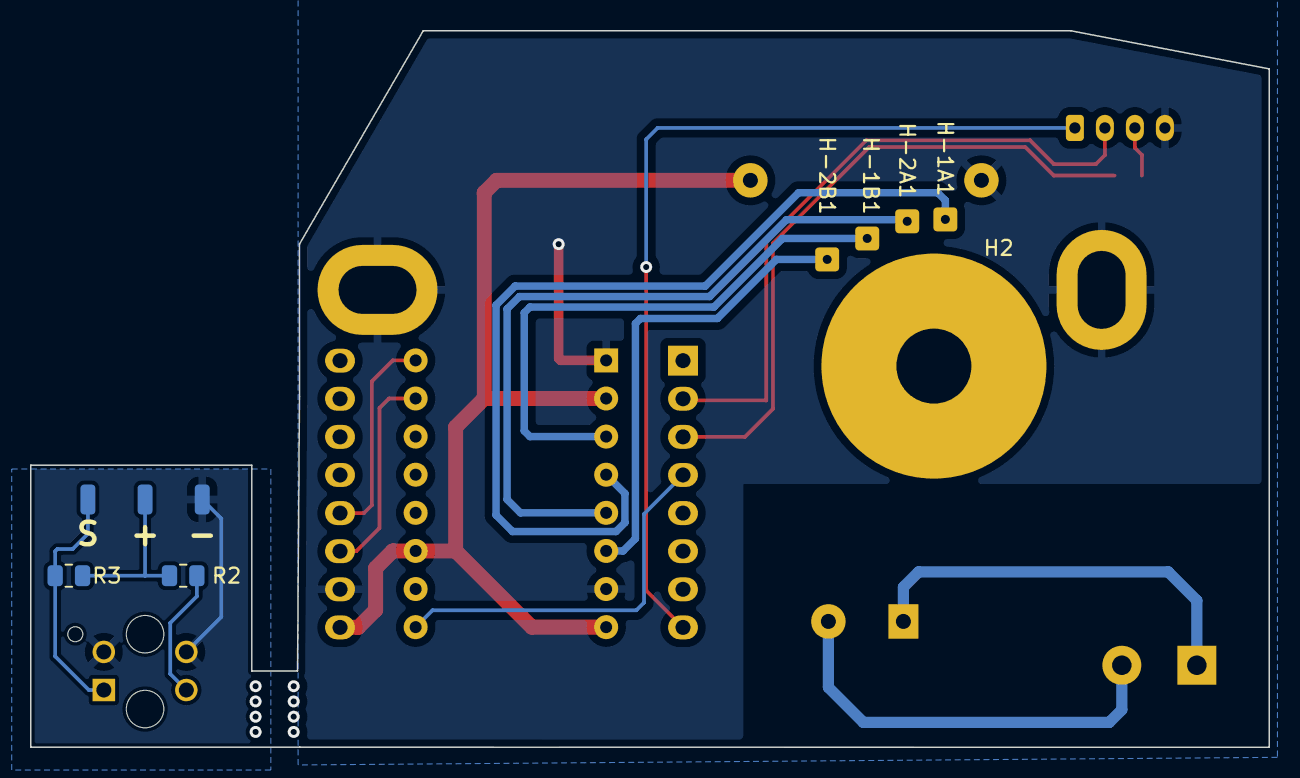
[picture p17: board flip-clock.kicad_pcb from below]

Board: 2 copper layers, 82.6 x 47.8 mm, 19 parts (6 on the bottom side), 19 nets.

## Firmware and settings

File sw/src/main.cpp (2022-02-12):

#include <Arduino.h>

#define ESP_DRD_USE_EEPROM true

#include <ArduinoOTA.h>
#include <DNSServer.h>
#include <ESP8266WebServer.h>
#include <ESP8266WiFi.h>
#include <ESP8266mDNS.h>
#include <ESP_DoubleResetDetector.h>
#include <WiFiManager.h>
#include <WiFiUdp.h>

#include <AceTime.h>

#include <list>

#define OTA 1

#if !defined(NTP_SERVER)
#define NTP_SERVER "pool.ntp.org"
#endif

#define DEBUG 1

#define STATS_ADDRESS 10
#define DRD_ADDRESS 4
#define EEPROM_MAGIC_NUMBER 0xdeadbeed
#define MAX_STEPS_PER_FLIP 40

typedef struct {
    uint32_t magicNumber;
    uint32_t uptimeSeconds;
    uint32_t uptimeSecondsTotal;
    uint32_t previousSecondsTotal;
    uint16_t reboots;
    uint16_t skipped;
    uint16_t skippedTotal;
    uint32_t previousSkippedTotal;
    uint32_t zoneId;
} statistics_t;

statistics_t globalStats;

DoubleResetDetector drd(DRD_ADDRESS, 0);

class Logger : public Print {

public:
    size_t write(uint8_t c)
    {
        if (c == '\n') {
            lastItems.push_back(currentLine);
            if (lastItems.size() > 100) {
                lastItems.pop_front();
            }
            currentLine = String("");
        } else {
            currentLine += (char)c;
        }
        return 1;
    }
    std::list<String> lastItems;

private:
    String currentLine = String("");
};

std::vector<int16_t> irValues;

Logger logger;

static const time_t EPOCH_2000_01_01 = 946684800;
static const unsigned long REBOOT_TIMEOUT_MILLIS = 5000;

using namespace ace_time;
using namespace ace_time::zonedbx;
static const int CACHE_SIZE = 3;
ExtendedZoneProcessorCache<1> zoneProcessorCache;
static ExtendedZoneProcessor localZoneProcessor;

ExtendedZoneManager zoneManager(
    zonedbx::kZoneRegistrySize,
    zonedbx::kZoneRegistry,
    zoneProcessorCache);

static TimeZone localZone = zoneManager.createForZoneInfo(&zonedbx::kZoneEurope_Berlin);

ESP8266WebServer server(80);

// /EN auf D5, D5 = 14
#define ENABLE 14
// STEP auf D4 = 2
#define STEP 2
// DIR auf D3 = 0
#define DIR 0

static uint16_t irPhotoDiodeBaseLine = analogRead(A0);
int16_t currentDisplayedTime = 9 * 60 + 44;
int16_t currentTime = 07 * 60 + 55;
bool fastMode = true;

int16_t upTriggeredAt = -1;
int16_t downTriggeredAt = -1;

void setCurrentTime();
void calculateBaseline();

void setupSntp()
{
    Serial.print(F("Configuring SNTP"));
    configTime(0 /*timezone*/, 0 /*dst_sec*/, NTP_SERVER);

    // Wait until SNTP stabilizes by ignoring values before year 2000.
    unsigned long startMillis = millis();
    while (true) {
        Serial.print('.'); // Each '.' represents one attempt.
        time_t now = time(nullptr);
        if (now >= EPOCH_2000_01_01) {
            Serial.println(F(" Done."));
            break;
        }

        // Detect timeout and reboot.
        unsigned long nowMillis = millis();
        if ((unsigned long)(nowMillis - startMillis) >= REBOOT_TIMEOUT_MILLIS) {
            Serial.println(F(" FAILED! Rebooting..."));
            drd.loop();
            delay(1000);
            ESP.reset();
        }

        delay(500);
    }
}

String secondsToString(uint32_t seconds)
{
    String result = "";
    if (seconds > 86400) {
        result = String(seconds / 86400) + "d ";
    }
    result = result + String((seconds / 3600) % 24) + "h ";
    result = result + String((seconds / 60) % 60) + "m ";
    result = result + String(seconds % 60) + "s";
    return result;
}

void handleRoot()
{
    int hour = (((1440 + currentDisplayedTime) / 60) % 24);
    int minute = (1440 + currentDisplayedTime) % 60;

    server.chunkedResponseModeStart(200, "text/html; charset=utf-8");

    String webpage = "<!DOCTYPE html><html><head>\n";
    webpage += "<title>FlipClock</title><style>\n";
    webpage += "body{margin-left:5em;margin-right:5em;font-family:sans-serif;font-size:14px;color:darkslategray;background-color:#EEE}h1{text-align:center}.info{width:100%;text-align:left;font-size:18pt}input,main,option,select,th{font-size:24pt;text-align:left}input{width:100%}input[type='submit']{width:min-content;float:right;text-align:right}main{font-size:16pt;vertical-align:middle}.info{line-height:2em}.info br{margin-left:3em}.logs{margin-top:2em;padding-top:2em;overflow-x:auto;border-top:black 2px solid}ul li{text-align:left}\n";
    webpage += ".graph {background-color: #EEE; font-size:0; overflow-x: auto; padding-bottom: 40px;} .bar { background-color: blueviolet; width: 1px; display: inline-block; } .active { background-color: green; }";
    webpage += "</style></head><body><h1>FlipClock by Wolfgang Jung</h1><div class='main'>\n";
    webpage += "<h2>Aktuell angezeigte Zeit:</h2>\n";
    webpage += "<form action=\"/set\" method=\"POST\"><table>\n";
    webpage += "<tr><th>Stunde:</th><td><input type=\"number\" name=\"hour\" value=\"" + String(hour) + "\" min=\"0\" max=\"23\"></td></tr>";
    webpage += "<tr><th>Minute:</th><td><input type=\"number\" name=\"minute\" value=\"" + String(minute) + "\" min=\"0\" max=\"59\"></td></tr>";
    webpage += "<tr><th>Zeitzone:</th><td><select name='zone'>\n";
    server.sendContent(webpage);

    uint16_t indexes[zonedbx::kZoneRegistrySize];
    ace_time::ZoneSorterByName<ExtendedZoneManager> zoneSorter(zoneManager);
    zoneSorter.fillIndexes(indexes, zonedbx::kZoneRegistrySize);
    zoneSorter.sortIndexes(indexes, zonedbx::kZoneRegistrySize);
    for (int i = 0; i < zonedbx::kZoneRegistrySize; i++) {
        ace_common::PrintStr<32> printStr;
        ExtendedZone zone = zoneManager.getZoneForIndex(indexes[i]);
        zone.printNameTo(printStr);
        webpage = "<option value='" + String(indexes[i]) + "'";
        if (zone.zoneId() == globalStats.zoneId) {
            webpage += " selected='selected'";
        }
        webpage += ">" + String(printStr.getCstr()) + "</option>\n";
        server.sendContent(webpage);
    }

    webpage = "</select></td></tr>";
    webpage += "<tr><th></th><td><input id='save' type=\"submit\" value=\"Speichern\"></td></tr></table></form><br/></div>\n";
    webpage += "<div class='info'>";
    webpage += "<div class='time'><h2>Aktuelle Zeit</h2><tt>";

    time_t localTime = time(nullptr);
    ZonedDateTime zonedDateTime = ZonedDateTime::forUnixSeconds(
        localTime, localZone);
    ace_common::PrintStr<60> currentTimeStr;
    zonedDateTime.printTo(currentTimeStr);

    webpage += String(currentTimeStr.getCstr()) + "</tt></div></br>\n";
    webpage += "<div class='stats'><h2>Stats</h2>\n";
    webpage += "Uptime:" + secondsToString(globalStats.uptimeSeconds) + "<br/>\n";
    webpage += "Uptime gesamt:" + secondsToString(globalStats.uptimeSecondsTotal) + "<br/>\n";
    webpage += "Skips :" + String(globalStats.skipped) + "<br/>\n";
    webpage += "Skips gesamt:" + String(globalStats.skippedTotal) + "<br/>\n";
    webpage += "Reboots:" + String(globalStats.reboots) + "<br/>\n";
    webpage += "Version: " + String(__TIMESTAMP__) + "<br/></div></div>\n";
    server.sendContent(webpage);

    if (logger.lastItems.size() > 0) {
        server.sendContent("<div class='logs'><h2>Logs</h2><ul>\n");

        for (std::list<String>::reverse_iterator line = logger.lastItems.rbegin();
             line != logger.lastItems.rend();
             line++) {
            server.sendContent("<li><pre>" + (*line) + "</pre></li>\n");
        }
        server.sendContent("</ul></div>");

        server.sendContent("<div class='graph'>\n");
        int idx = 0;
        for (uint16_t val : irValues) {
            bool visible = (downTriggeredAt < 0 && upTriggeredAt < 0) || (idx > max(downTriggeredAt, (int16_t)(upTriggeredAt - 100)) - 200 && idx < upTriggeredAt + 200);
            if (!visible) {
                idx++;
                continue;
            }
            if (idx == upTriggeredAt || idx == downTriggeredAt) {
                server.sendContent("<div style='height: " + String(val) + "px' class='bar active'></div>\n");
            } else {
                server.sendContent("<div style='height: " + String(val) + "px' class='bar'></div>\n");
            }
            idx++;
        }
        server.sendContent("</div>");
    }

    server.sendContent("</body></html>\n");

    server.chunkedResponseFinalize();
}

void handleSet()
{
    int hour = server.arg("hour").toInt();
    int minute = server.arg("minute").toInt();
    int zoneIdx = server.arg("zone").toInt();
    currentDisplayedTime = (hour * 60 + minute) % 1440;

    localZone = zoneManager.createForZoneIndex(zoneIdx);
    if (localZone.isError() == false) {
        globalStats.zoneId = localZone.getZoneId();
        EEPROM.put(STATS_ADDRESS, globalStats);
        EEPROM.commit();
    }

    server.sendHeader("Location", "/");
    server.send(302, "text/plain", "");
}

void readFromEEProm()
{
    // EEPROM.begin(sizeof(statistics_t));
    // Already got begin() called by DRD constructor
    EEPROM.get(STATS_ADDRESS, globalStats);
    if (globalStats.magicNumber != EEPROM_MAGIC_NUMBER) {
        globalStats.magicNumber = EEPROM_MAGIC_NUMBER;
        globalStats.reboots = 0;
        globalStats.skipped = 0;
        globalStats.skippedTotal = 0;
        globalStats.previousSkippedTotal = 0;
        globalStats.uptimeSeconds = 0;
        globalStats.uptimeSecondsTotal = 0;
        globalStats.previousSecondsTotal = 0;
        globalStats.zoneId = zonedbx::kZoneIdEurope_Berlin;
        EEPROM.put(STATS_ADDRESS, globalStats);
    }
    globalStats.previousSecondsTotal = globalStats.uptimeSecondsTotal;
    globalStats.previousSkippedTotal = globalStats.skippedTotal;
    localZone = zoneManager.createForZoneId(globalStats.zoneId);
    if (localZone.isError()) {
        globalStats.zoneId = zonedbx::kZoneIdEurope_Berlin;
        localZone = zoneManager.createForZoneId(globalStats.zoneId);
        EEPROM.put(STATS_ADDRESS, globalStats);
    }
    globalStats.uptimeSeconds = 0;
    globalStats.skipped = 0;

    Serial.print("Using Timezone: ");
    localZone.printTo(Serial);
    Serial.println();
    EEPROM.commit();
}

void setup()
{
    Serial.begin(115200);
    readFromEEProm();
    globalStats.uptimeSeconds = 0;

    Serial.println(F("\nStarting FlipClock 2022 - Wolfgang Jung / Ideas In Logic\n"));

    pinMode(ENABLE, OUTPUT);
    pinMode(STEP, OUTPUT);
    pinMode(DIR, OUTPUT);
    pinMode(D0, OUTPUT);
    digitalWrite(D0, HIGH);

    digitalWrite(ENABLE, HIGH);
    calculateBaseline();

    WiFiManager wiFiManager;

    if (drd.detectDoubleReset()) {
        digitalWrite(ENABLE, LOW);
        Serial.println(F("Reset WiFi configuration"));
        wiFiManager.resetSettings();
        wiFiManager.startConfigPortal("FlipClock", "");
    }

#ifdef DEBUG
    logger.println(F("Trying to connect to known WiFi"));
#endif
    if (!wiFiManager.autoConnect("FlipClock")) {
        digitalWrite(ENABLE, LOW);
        Serial.println("failed to connect and hit timeout");
        delay(3000);
        digitalWrite(ENABLE, HIGH);
        // reset and try again, or maybe put it to deep sleep
        ESP.reset();
    }

    if (MDNS.begin("flipclock")) { // Start the mDNS responder for esp8266.local
#ifdef DEBUG
        logger.println("mDNS responder started");
#endif
    } else {
        logger.println("Error setting up MDNS responder!");
    }

    digitalWrite(ENABLE, LOW);
    server.on("/", HTTP_GET, handleRoot);
    server.on("/set", HTTP_POST, handleSet);
    server.onNotFound([]() {
        server.send(404, "text/plain", "404: Not found");
    });
    server.begin();

    globalStats.reboots++;
    EEPROM.put(STATS_ADDRESS, globalStats);

    setupSntp();
    setCurrentTime();

    // assume short outage
    currentDisplayedTime = currentTime;

#ifdef OTA
    // Port defaults to 8266
    ArduinoOTA.setPort(8266);

    // Hostname defaults to esp8266-[ChipID]
    ArduinoOTA.setHostname("flipclock");

    // No authentication by default
    // ArduinoOTA.setPassword("admin");

    ArduinoOTA.onStart([]() {
        String type;
        if (ArduinoOTA.getCommand() == U_FLASH) {
            type = "sketch";
        } else { // U_FS
            type = "filesystem";
        }
        // NOTE: if updating FS this would be the place to unmount FS using FS.end()
        Serial.println("Start updating " + type);
    });
    ArduinoOTA.onEnd([]() {
        Serial.println("\nEnd");
    });
    ArduinoOTA.onProgress([](unsigned int progress, unsigned int total) {
#ifdef DEBUG
        logger.printf("Progress: %u%%\r", (progress / (total / 100)));
#endif
    });
    ArduinoOTA.onError([](ota_error_t error) {
        Serial.printf("Error[%u]: ", error);
        if (error == OTA_AUTH_ERROR) {
            Serial.println("Auth Failed");
        } else if (error == OTA_BEGIN_ERROR) {
            Serial.println("Begin Failed");
        } else if (error == OTA_CONNECT_ERROR) {
            Serial.println("Connect Failed");
        } else if (error == OTA_RECEIVE_ERROR) {
            Serial.println("Receive Failed");
        } else if (error == OTA_END_ERROR) {
            Serial.println("End Failed");
        }
    });
    ArduinoOTA.begin();
#endif
    digitalWrite(ENABLE, HIGH);
}

void setCurrentTime()
{
    time_t localTime = time(nullptr);
    ZonedDateTime zonedDateTime = ZonedDateTime::forUnixSeconds(
        localTime, localZone);
    currentTime = zonedDateTime.minute() + zonedDateTime.hour() * 60;
    if (zonedDateTime.second() > 58) {
        currentTime += 1;
    }
}

void calculateBaseline()
{
    int base = 0;
    for (int x = 0; x < 10; x++) {
        base = base + analogRead(A0);
        delayMicroseconds(10);
    }
    irPhotoDiodeBaseLine = base / 10;
}

void advance()
{
    int16_t minValue = 1024;
    int16_t maxValue = 0;
    bool minuteDisplayFlipped = false;
    uint16_t triggerCount = 0;
    uint16_t minimumAt = 0;
    uint16_t maximumAt = 0;
    upTriggeredAt = -1;
    downTriggeredAt = -1;
    int16_t currentIrReading = 0;

    digitalWrite(ENABLE, LOW);
    digitalWrite(DIR, HIGH);
    calculateBaseline();
    maxValue = 0;
    minValue = 1024;

    irValues.clear();
    irValues.resize(0);

    for (uint16_t stepperMotorSteps = 0; stepperMotorSteps < 60; stepperMotorSteps++) {
        if (!minuteDisplayFlipped) {
            digitalWrite(STEP, HIGH);
            delayMicroseconds(1);
            digitalWrite(STEP, LOW);
        }
        for (int count = 0; count < 30; count++) {
            currentIrReading = analogRead(A0);
            irValues.push_back(currentIrReading);
            if (currentIrReading < minValue) {
                minimumAt = stepperMotorSteps;
                minValue = currentIrReading;
            }
            if (currentIrReading > maxValue) {
                maximumAt = stepperMotorSteps;
                maxValue = currentIrReading;
            }
            int historyElements = irValues.size();
            if (historyElements > 300) {
                // small rising edge if at least 60% of highest swing so far but also at least 10 ticks high
                bool smallUp = downTriggeredAt == -1 && // no falling edge detected so far
                    stepperMotorSteps > 20 && // at least some steps already done
                    10 * (currentIrReading - irValues[historyElements - 50]) > 6 * max(10, maxValue - minValue);
                bool up = smallUp || currentIrReading - irValues[historyElements - 100] > 50;
                bool down = irValues[historyElements - 100] - currentIrReading > 50;
                if (up || down) {
                    triggerCount++;
                    if (down && downTriggeredAt == -1) {
                        downTriggeredAt = historyElements;
                    }
                    if (up && upTriggeredAt == -1) {
                        upTriggeredAt = historyElements;
                    }
                    minuteDisplayFlipped = true;
                }
            }
            delayMicroseconds(100);
        }
    }

    if (triggerCount <= 5) {
        globalStats.skipped++;
    } else {
        currentDisplayedTime++;
    }

    for (std::vector<int16_t>::iterator it = irValues.begin(); it != irValues.end(); it++) {
        *it = *it - minValue;
    }

    if (currentDisplayedTime >= 1440) {
        currentDisplayedTime -= 1440;
    }
#ifdef DEBUG
    time_t localTime = time(nullptr);
    ZonedDateTime zonedDateTime = ZonedDateTime::forUnixSeconds(
        localTime, localZone);
    ace_common::PrintStr<64> currentTimeStr;
    zonedDateTime.printTo(currentTimeStr);

    logger.printf("%s - %02d:%02d - triggerCount=%d up=%d down=%d val=%d min=%d@%d max=%d@%d base=%d\n",
        currentTimeStr.getCstr(),
        (((1440 + currentDisplayedTime) / 60) % 24),
        (1440 + currentDisplayedTime) % 60,
        triggerCount, upTriggeredAt, downTriggeredAt, currentIrReading, minValue, minimumAt, maxValue, maximumAt, irPhotoDiodeBaseLine);
#endif
}

template <int T>
void runEvery(void (*f)())
{
    static unsigned long lastMillis = millis();
    unsigned long now = millis();
    if (now >= lastMillis + T) {
        // run every T milli-seconds
        f();
        lastMillis = millis();
    }
}

void loop()
{
    // WebServer should react..
    server.handleClient();
#ifdef OTA
    // OTA the same
    ArduinoOTA.handle();
#endif

    // The main time-handling code, wait at least 1 second between flips
    runEvery<1000>([]() {
        if (currentDisplayedTime < currentTime) {
            advance();
        } else if (currentDisplayedTime == currentTime) {
            digitalWrite(ENABLE, HIGH);
            fastMode = false;
        } else { // currentDisplayedTime > currentTime
            if (currentTime >= 1 * 60 && currentTime <= 6 * 60) {
                // do nothing in the night
                fastMode = false;
            } else if (currentDisplayedTime > currentTime + 10) {
                fastMode = true;
                currentDisplayedTime -= 1440;
            }
        }
    });

    // every half second -> housekeeping of time and name
    runEvery<500>([]() {
        globalStats.uptimeSeconds = (millis() / 1000);
        globalStats.uptimeSecondsTotal = globalStats.previousSecondsTotal + globalStats.uptimeSeconds;
        globalStats.skippedTotal = globalStats.previousSkippedTotal + globalStats.skipped;
        setCurrentTime();
        drd.loop();
        MDNS.update();
    });

    // every 15 minutes -> store stats
    runEvery<1000 * 15 * 60>([]() {
        EEPROM.put(STATS_ADDRESS, globalStats);
        EEPROM.commit();
    });
}

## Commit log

2021-04-09 Added 3D models
    [flip-clock.kicad_pcb, flip-clock.kicad_sch, tmc2100.step]
2021-04-19 Move kicad files to own directory
    [flip-clock.kicad_pcb, flip-clock.kicad_sch, tmc2100.step]
2021-05-09 Layout without choke
    [flip-clock.kicad_pcb, flip-clock.kicad_sch]
2021-05-11 Trapezoid Layout, Transformer in Front
    [flip-clock.kicad_pcb]
2021-05-11 Wrong side populated
    [flip-clock.kicad_pcb, flip-clock.kicad_sch]
2021-05-11 Correct side
    [flip-clock.kicad_pcb, flip-clock.kicad_sch]
2021-05-13 Redesign after fitting probe
    [flip-clock.kicad_pcb]
2021-05-15 JST Connector for IR and hour
    [flip-clock.kicad_pcb, flip-clock.kicad_sch]
2021-05-15 Lichtschranke hinzu
    [TCRT5000.stp]
2021-05-15 second PCB-Part for IR
    [flip-clock.kicad_pcb, flip-clock.kicad_sch]
2021-06-03 Switched to TMC
    [flip-clock.kicad_pcb]
2021-06-07 step until IR detects flip
    [main.cpp]
2021-06-07 Missing net for flipped IR sensor
    [flip-clock.kicad_pcb]
2022-01-24 Upgraded to kicad 6.0
    [flip-clock.kicad_pcb]
2022-01-24 Adds correct handling of IR-Sensor and wifi
    [main.cpp]
2022-01-24 New kicad version
    [flip-clock.kicad_sch]
2022-01-24 Adds double-reset and OTA
    [main.cpp]
2022-01-25 Adds missing MDNS update call
    [main.cpp]
2022-01-28 Use 3v3 as stable power supply for IR-Sensor
    [flip-clock.kicad_pcb, flip-clock.kicad_sch]
2022-01-28 Adds Logging for debugging random flips
    [main.cpp]
2022-02-03 Adds better assumption for detecting flipped minutes
    [main.cpp]
2022-02-05 Improves flip detection by measuring irValue/dt
    [main.cpp]
2022-02-05 Assume, that missed triggers alreday flipped the minutes
    [main.cpp]
2022-02-06 Adds detection of rising and falling edge
    [flip-clock.kicad_pcb, flip-clock.kicad_sch]
2022-02-10 Retry, if triggerCount too small
    [main.cpp]
